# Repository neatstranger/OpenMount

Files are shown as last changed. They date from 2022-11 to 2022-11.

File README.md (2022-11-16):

# OpenMount
An open source Equatorial tracking mount for visual astronomy and astrophotography.
OpenMount_Iso View

## Specs

### Hardware 
**Stepper Motors:**
Nema 17 Bipolar 0.9deg 46Ncm [Buy Here](https://www.omc-stepperonline.com/nema-17-bipolar-0-9deg-46ncm-65-1oz-in-2a-2-9v-42x42x48mm-4-wires-17hm19-2004s)

**Motor Drivers:**
Looking for 1/32 Microsteps at a relatively low cost. Probably something from the 3D printer world.

**Gearbox:**
Gearbox - Ratio 162:1, 3mm Belt Width. 3D Printed Pulleys. Heat set inserts for shaft adaption.

### Resolution Of Mount
Stock Resolution 20 Arc Seconds Per Step.

@1/32 Microsteps: 0.625 Arc Seconds Per Step.

@1/64 Microsteps: 0.3125 Arc Seconds Per Step

@1/128 Microsteps: 0.15625 Arc Seconds Per Step

# Part List
The mount uses a combination of purchased steel parts, fabricated aluminum(cut/bend), and 3D printed parts. With a bit of work, I may be able to replace some of the gearbox planes with either carbon fiber, or 3D printed to reduce cost and weight.

## Cut/Bent - (Flat Files) - [SendCutSend](https://sendcutsend.com/)
*Modeled With 5052 Aluminum 0.187"-4.7mm, 0.43, 6.35* [Thickness, K Factor, Bend Radius](https://sendcutsend.com/materials/5052-aluminum/)

Polar Aligment Fork - Base QTY: 1

Polar Alignment Fork - Right Arm QTY: 1

Polar Aligment Fork - Left Arm QTY: 1

Polar Aligment - QTY: 1

Gearbox Housing - Motor Mount Plane - QTY 2

Gearbox Housing - Mid Plane - QTY 2

Gearbox Housing - Far Plane - QTY 2

Declination Motor Mount - QTY 1

## Purchased Items
Stepper Motor - NEMA 17 - 0.9deg - 2.0A [Stepper Online](https://www.omc-stepperonline.com/full-d-cut-shaft-nema-17-bipolar-0-9deg-46ncm-65-1oz-in-2a-2-9v-42x42x48mm-4-wires-17hm19-2004s1)

Stepper Driver [Source](https://www.pololu.com/product/3764)

5mm Shaft Ball Bearings - QTY 12 [McMaster-Carr](https://www.mcmaster.com/7804K109/)

5mm Shaft Collar - QTY 2 [McMaster-Carr](https://www.mcmaster.com/9520T2/)

5mm Shaft - QTY 1 [McMaster-Carr](https://www.mcmaster.com/1265K46/)

203mm Timing Belt - QTY 2 [McMaster-Carr](https://www.mcmaster.com/5027N22/)

143mm Timing Belt - QTY 4 [McMaster-Carr](https://www.mcmaster.com/5027N17/)

12mm Shaft Collar - QTY 1 [McMaster-Carr](https://www.mcmaster.com/6063K16/)

12mm Shaft - QTY 1 [McMaster-Carr](https://www.mcmaster.com/1482K19/)

M2 Threaded Inserts For Plastic - [McMaster-Carr](https://www.mcmaster.com/94459A110/)

M3 Threaded Inserts For Plastic - [McMaster-Carr](https://www.mcmaster.com/94459A130/)

Various M3, M4, M5, and M8 Bolts, Nuts and Washers

## 3D Printed Files

60 Tooth Pulley - Pitch Diameter 38.8mm - QTY 6

11 Tooth Pulley - Pitch Diameter 7.1mm - QTY 6

Large Plane Spacer - QTY 4

Small Plane Spacer - QTY 4

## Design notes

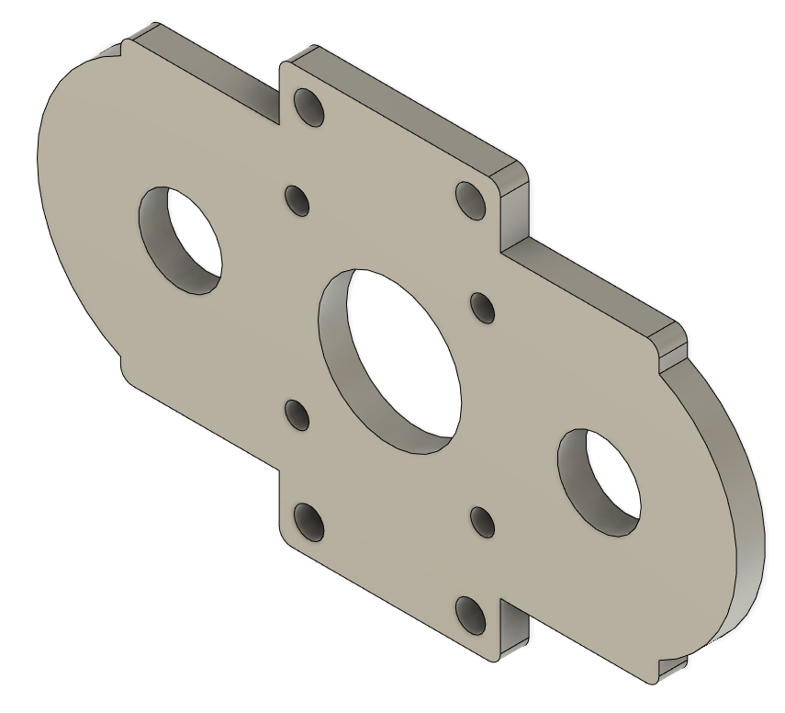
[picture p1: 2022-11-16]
Images/Motor Mount Plane_ISO.png

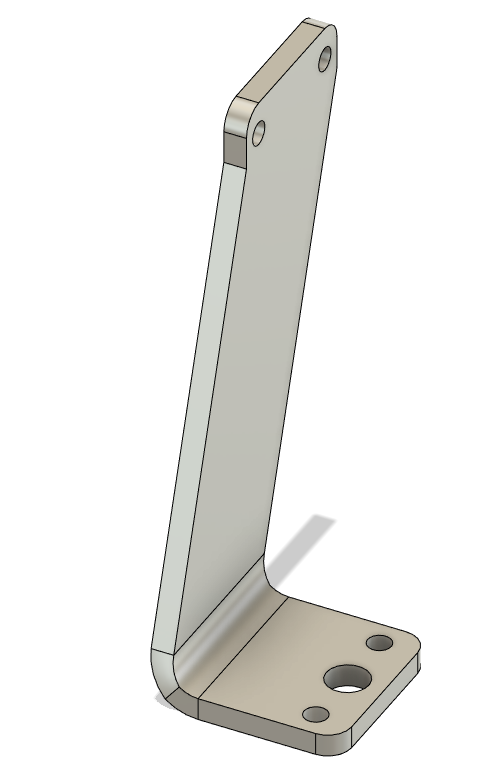
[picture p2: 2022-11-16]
Images/Polar Alignment Fork - Left Arm_ISO.png

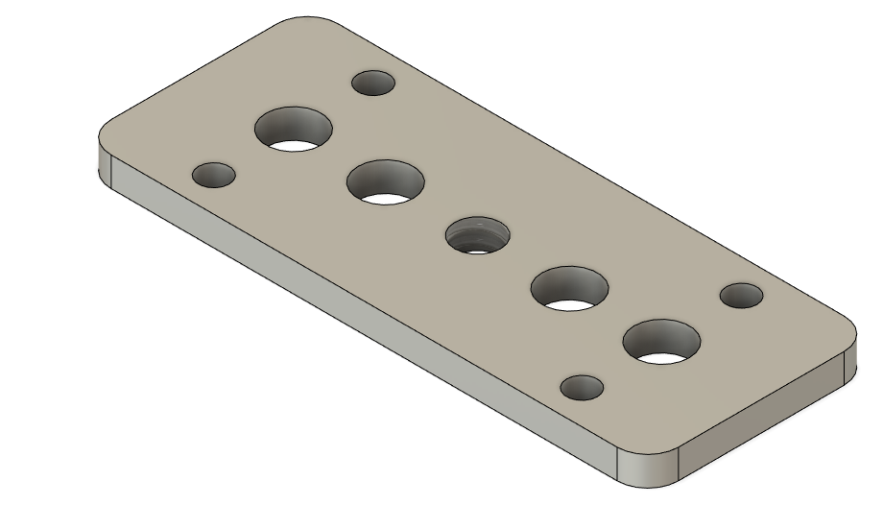
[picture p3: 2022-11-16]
Images/Tripod Mount Base_ISO.png

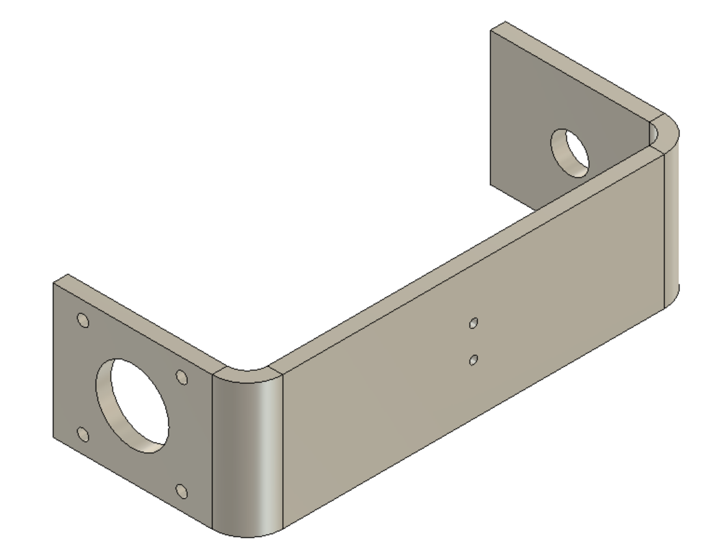
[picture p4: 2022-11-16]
Images/Declination Motor Mount_ISO.png

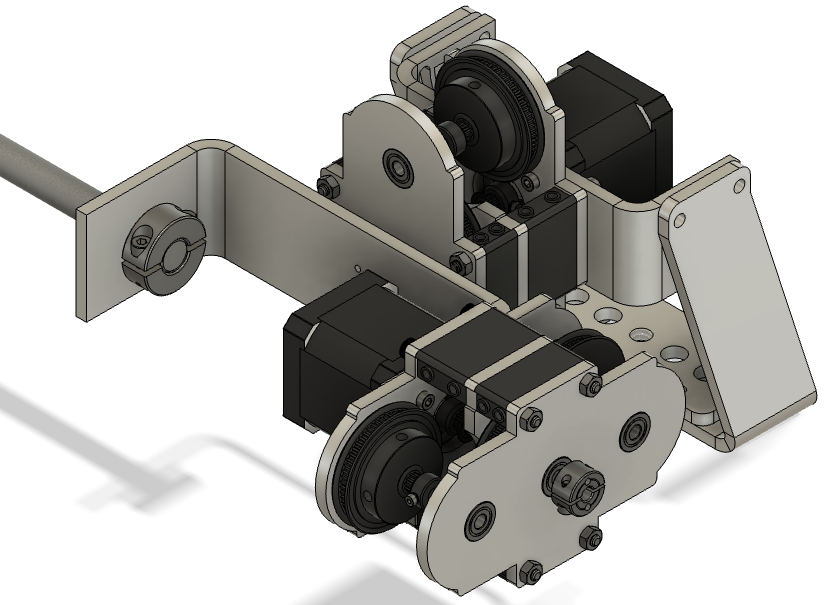
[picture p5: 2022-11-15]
Images/OpenMount_ISO.png

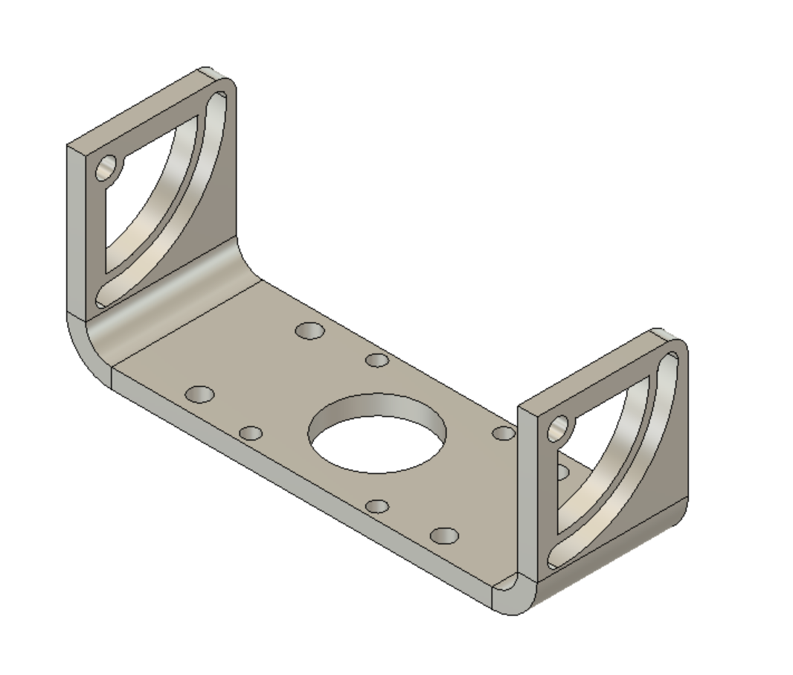
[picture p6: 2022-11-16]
Images/Polar Align Bracket_ISO.png

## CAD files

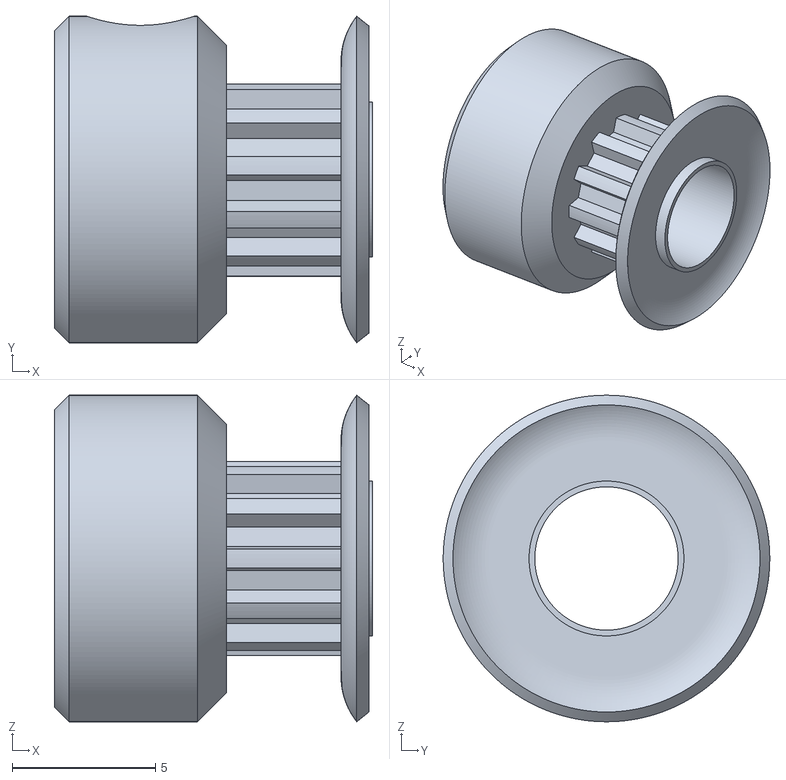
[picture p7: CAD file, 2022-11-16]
Part Files/3D Printed Parts/11 Tooth Pulley/11 Tooth Pulley.stl
11.1 x 11.4 x 11.4

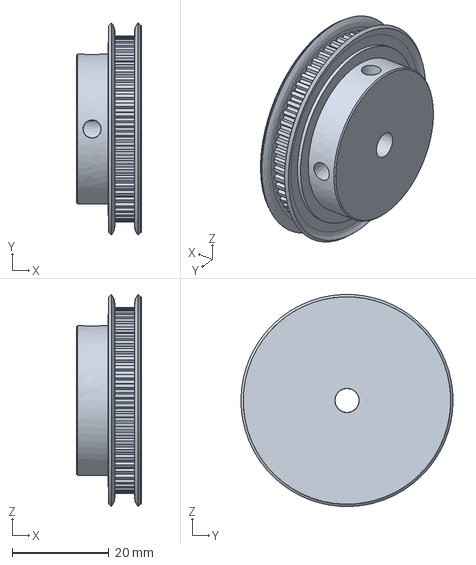
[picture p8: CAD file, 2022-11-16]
Part Files/3D Printed Parts/60 Tooth Pulley/60 Tooth Pulley.iges
13.5 x 43.9 x 43.9 mm

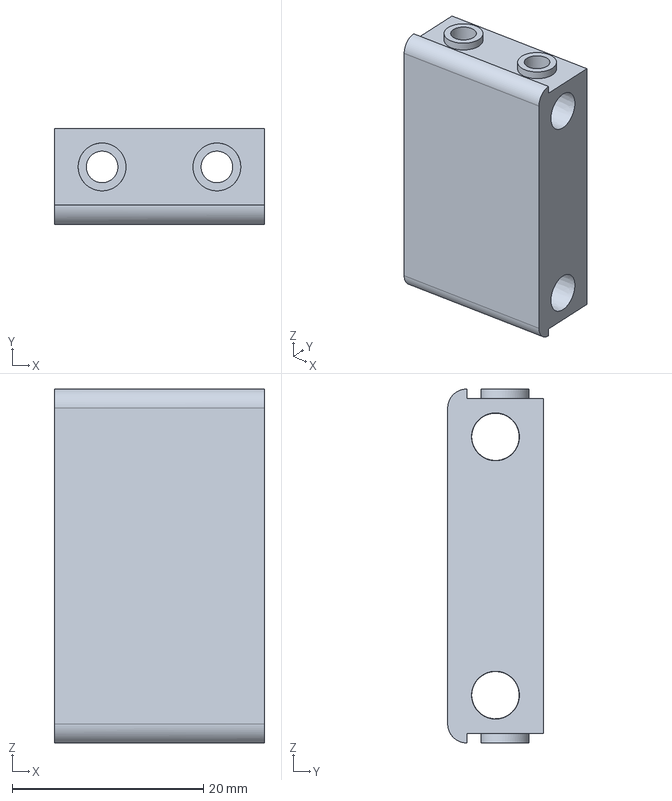
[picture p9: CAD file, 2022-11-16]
Part Files/3D Printed Parts/Large Spacer/Large Spacer v4.iges
22.0 x 10.0 x 37.0 mm

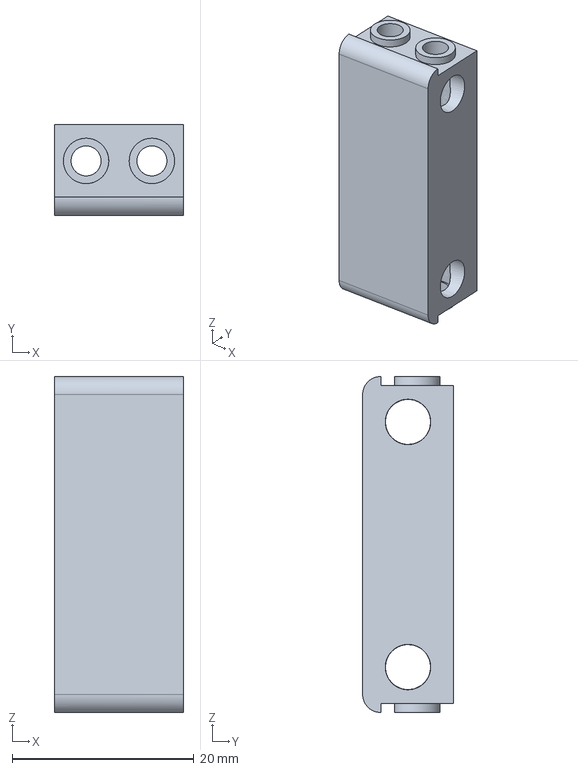
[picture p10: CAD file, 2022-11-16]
Part Files/3D Printed Parts/Small Spacer/Small Spacer v4.iges
14.3 x 10.0 x 37.0 mm

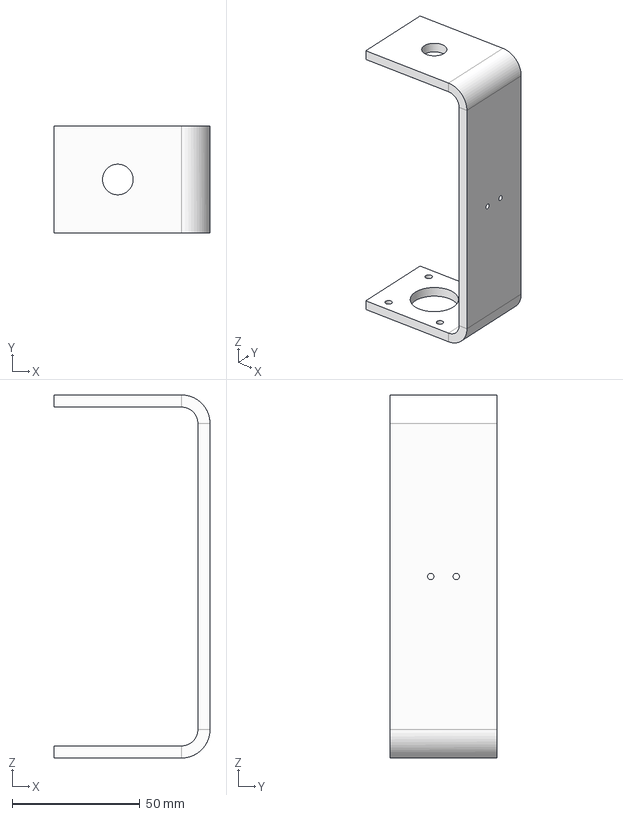
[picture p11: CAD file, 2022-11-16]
Part Files/Cut and Bent Parts/Declination Motor Mount/Declination Motor Mount v3.iges
61.1 x 42.0 x 142.2 mm

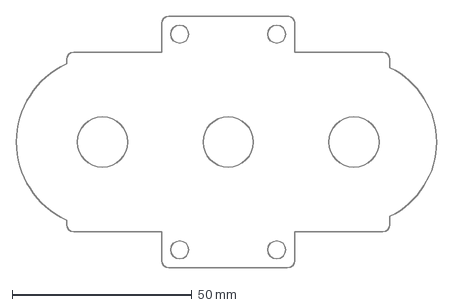
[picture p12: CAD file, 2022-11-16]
Part Files/Cut and Bent Parts/Gearbox Housing/Far Plane/Far Plane.dxf
117.0 x 70.0 mm

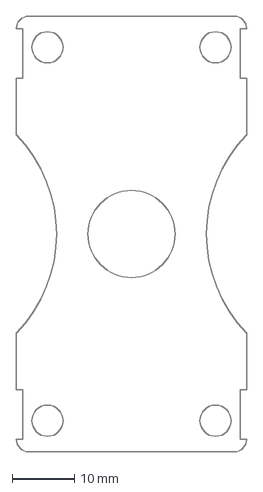
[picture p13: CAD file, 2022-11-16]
Part Files/Cut and Bent Parts/Gearbox Housing/Mid Plane/Mid Plane.dxf
37.0 x 70.0 mm

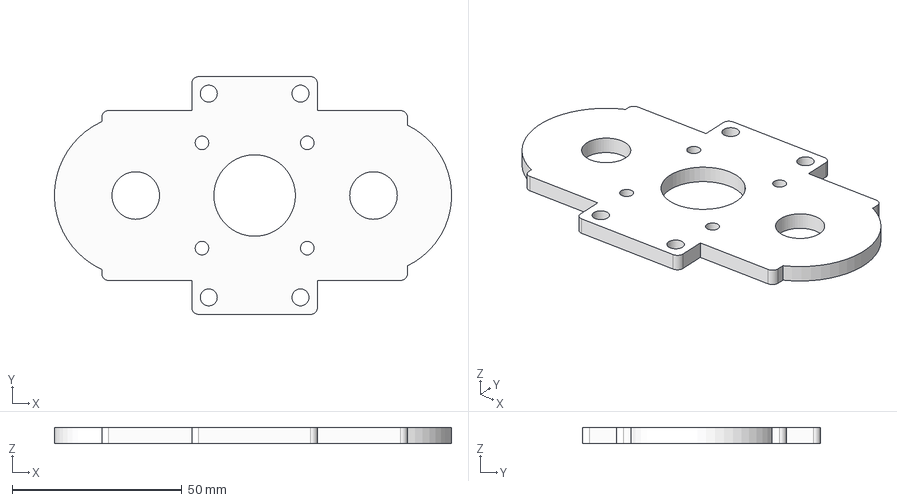
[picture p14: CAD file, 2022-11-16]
Part Files/Cut and Bent Parts/Gearbox Housing/Motor Mount Plane/Gearbox Housing - Motor Mount Plane v3.iges
116.9 x 70.0 x 4.75 mm

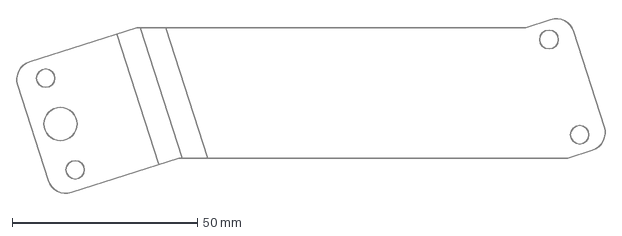
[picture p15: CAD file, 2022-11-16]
Part Files/Cut and Bent Parts/Polar Alignment Fork - Left Arm/Polar Alignment Fork - Left Arm.dxf
159.1 x 48.3 mm

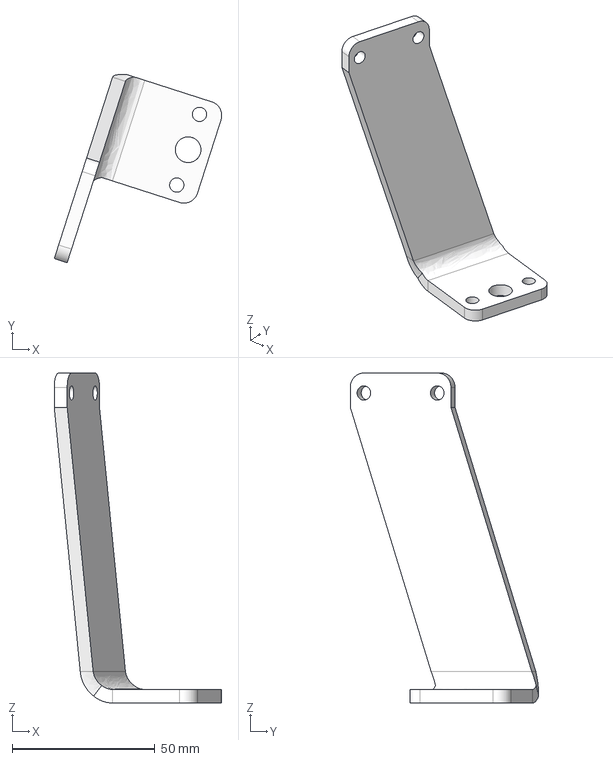
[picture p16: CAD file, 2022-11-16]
Part Files/Cut and Bent Parts/Polar Alignment Fork - Right Arm/Polar Alignment Fork - Right Arm v4.iges
58.7 x 66.0 x 115.6 mm

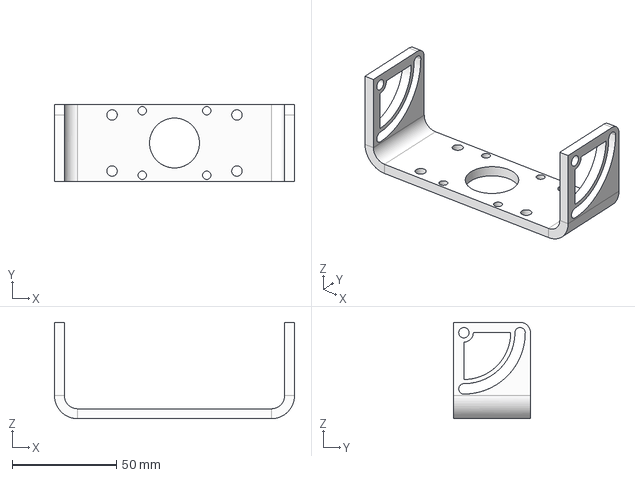
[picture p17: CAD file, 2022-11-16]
Part Files/Cut and Bent Parts/Polar Alignment/Polar Aligmnet v3.iges
115.4 x 37.0 x 46.3 mm

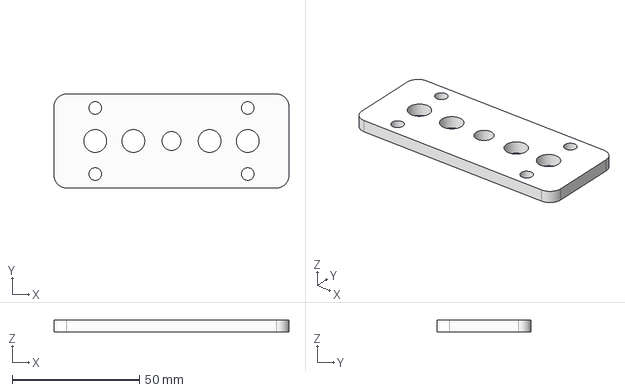
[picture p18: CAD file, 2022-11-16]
Part Files/Cut and Bent Parts/Tripod Base/Tripod Base v5.iges
92.4 x 37.0 x 4.75 mm

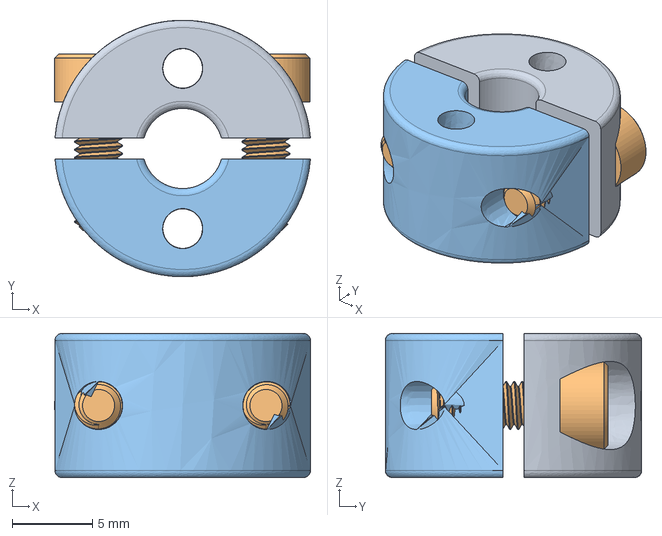
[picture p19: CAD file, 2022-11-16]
Part Files/Purchased Parts - Modified/9520T2_Clamping Two-Piece Shaft Collar/9520T2_Clamping Two-Piece Shaft Collar v1.iges
16.0 x 16.0 x 9.00 mm

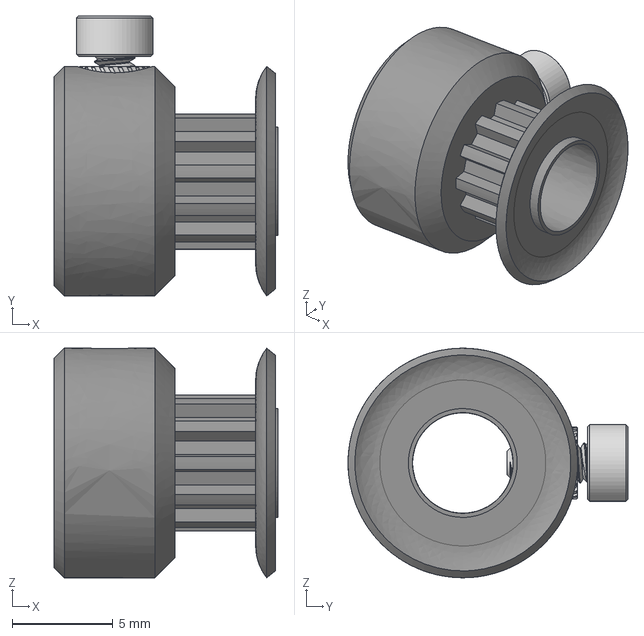
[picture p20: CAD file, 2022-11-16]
Part Files/3D Printed Parts/11 Tooth Pulley/Small Pulley - 3mm Belt v2.iges
11.1 x 13.9 x 11.4 mm

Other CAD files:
Part Files/Cut and Bent Parts/Declination Motor Mount/Declination Motor Mount.dxf
Part Files/Cut and Bent Parts/Gearbox Housing/Far Plane/Gearbox Housing - Far Plane v3.iges
Part Files/Cut and Bent Parts/Gearbox Housing/Mid Plane/Gearbox Housing - Mid Plane v3.iges
Part Files/Cut and Bent Parts/Gearbox Housing/Motor Mount Plane/Motor Mount Plane.dxf
Part Files/3D Printed Parts/11 Tooth Pulley/11 Tooth Pulley.f3z
Part Files/3D Printed Parts/11 Tooth Pulley/Original McMaster Files/1375K172_MXL Series Timing Belt Pulley.IGS
Part Files/3D Printed Parts/11 Tooth Pulley/Original McMaster Files/1375K172_MXL Series Timing Belt Pulley.SLDPRT
Part Files/3D Printed Parts/11 Tooth Pulley/Original McMaster Files/1375K172_MXL Series Timing Belt Pulley.STEP
Part Files/3D Printed Parts/11 Tooth Pulley/Small Pulley - 3mm Belt v2.3mf
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

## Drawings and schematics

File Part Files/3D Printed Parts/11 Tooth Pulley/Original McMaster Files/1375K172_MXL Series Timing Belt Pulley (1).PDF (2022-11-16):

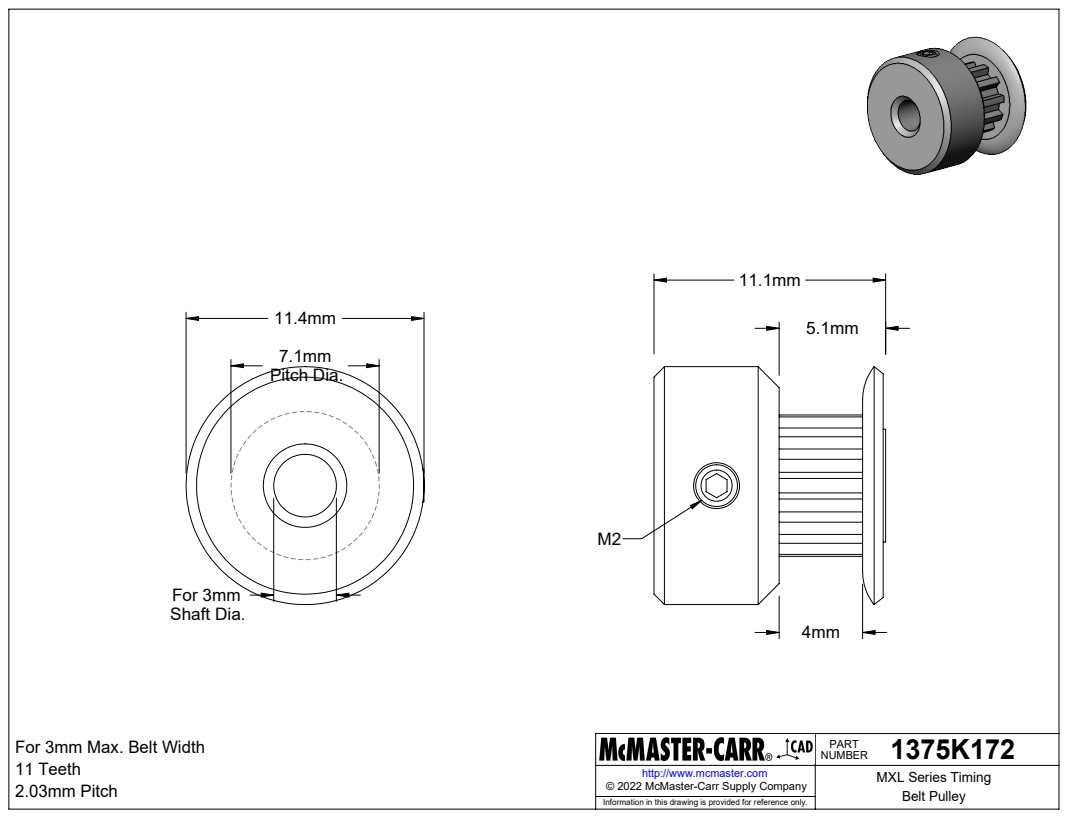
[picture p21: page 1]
For 3mm Shaft Dia.; Pitch Dia.; 2.03mm Pitch; Belt Pulley © 2022 McMaster-Carr Supply Company

1375K172 PART NUMBER

For 3mm Max. Belt Width
11 Teeth

http://www.mcmaster.com | MXL Series Timing

Information in this drawing is provided for reference only.

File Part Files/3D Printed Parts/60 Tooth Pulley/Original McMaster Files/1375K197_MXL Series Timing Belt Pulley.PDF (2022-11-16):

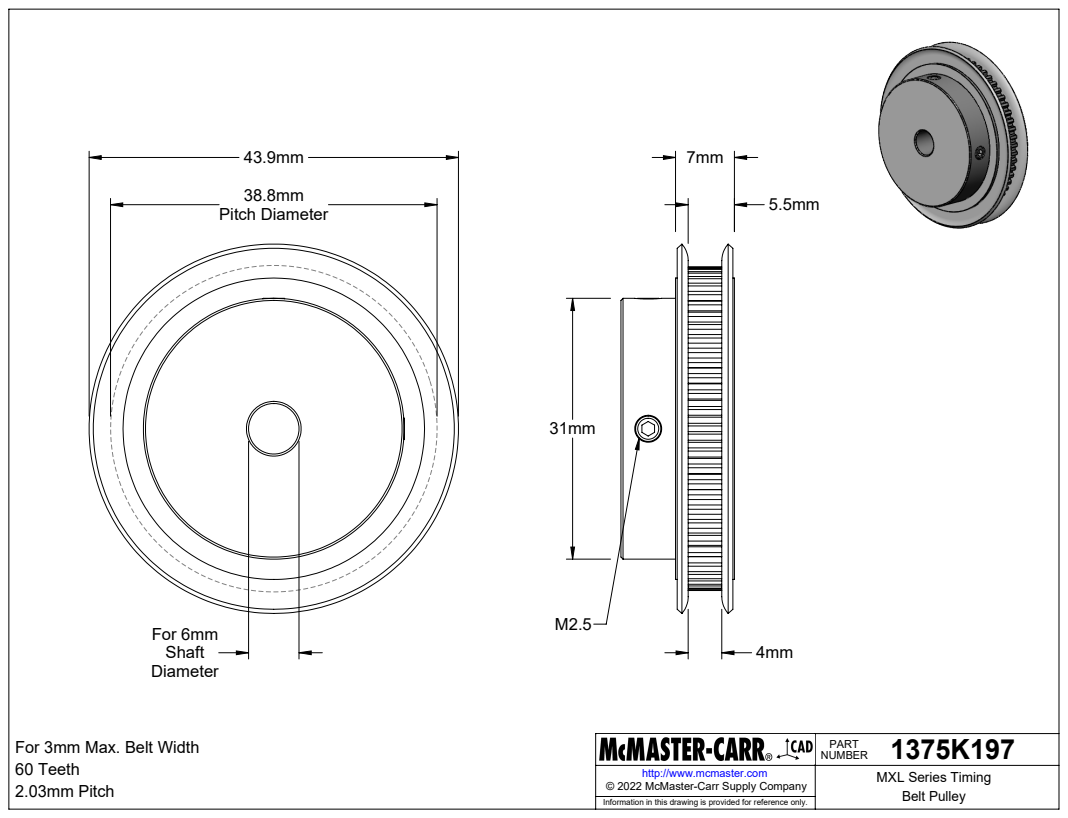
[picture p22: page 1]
For 6mm; Pitch Diameter; 2.03mm Pitch; Belt Pulley © 2022 McMaster-Carr Supply Company

1375K197 PART NUMBER

For 3mm Max. Belt Width
60 Teeth

http://www.mcmaster.com | MXL Series Timing

Information in this drawing is provided for reference only.

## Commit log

2022-11-15 Updated Readme
    Got the base specs of the mount put up.
2022-11-16 Working On Uploading All Files
    [11 Tooth Pulley.f3z, 11 Tooth Pulley.stl, 1375K197_MXL Series Timing Belt Pulley.IGS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]
2022-11-16 First Full Dump of All Files
    [11 Tooth Pulley.f3z, 11 Tooth Pulley.stl, 1375K172_MXL Series Timing Belt Pulley.IGS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]
